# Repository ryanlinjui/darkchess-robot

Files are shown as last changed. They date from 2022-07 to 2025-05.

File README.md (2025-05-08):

> *"The project has been re-developing and refactoring since now." - 2024.11.12*  
> *"Now 'ONLY Brain Feature' is waiting for been completed......" - 2025.04.05*

# Darkchess Robot

<div align="center">

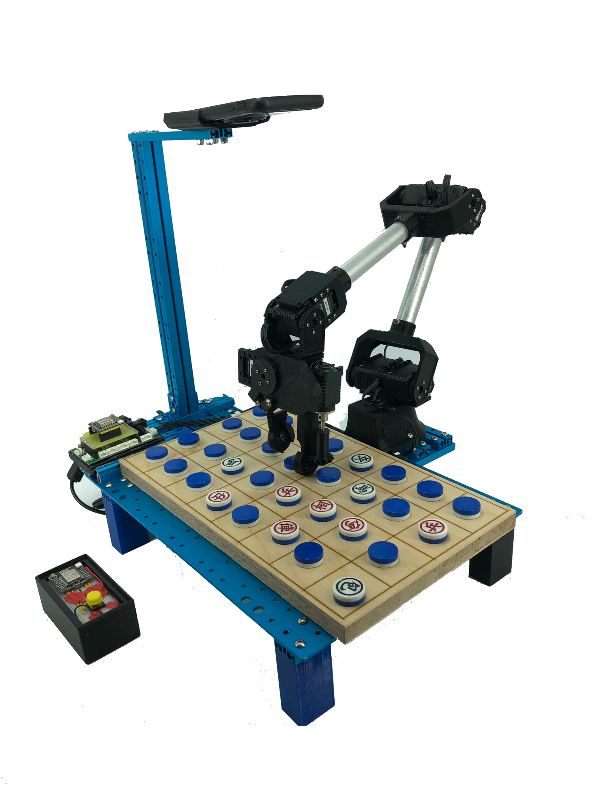
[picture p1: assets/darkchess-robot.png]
darkchess-robot
<br>

<br>
<br>
</div>

# 🤖 Demo

<div align="center">
  demo1
  demo2
</div>

# 💡 Getting Started
### Setup
Use [pixi](https://github.com/prefix-dev/pixi) to set up the development environment:

```
pixi shell
```

### Run Darkchess Robot System with Specific Mode
```bash
# Run Robot Server along with Website Monitor
python app.py --robot

# Run API Server of 'brain' & 'eye' Only
python app.py --api     
```
> Go [`config.py`](./config.py) to configure app settings before running server.

<div align="center">
  monitor
  sample-board
</div>

# 🚀 Features
## Brain - AI Engine for Darkchess Board Game
TBA......

## Eye – Real-World Detection and Recognition of Darkchess Board States
- **Model Architecture:** VGGNet-based darkchess board recognition
- **Training Accuracy:** 99.9%
- **Training Loss:** 7.2336e-06
- **Real-world Test Success Rate:** 98.9%

> For Eye training/testing script, refer to [`eye_train.ipynb`](./eye_train.ipynb).  
> Detailed model information is available on [Huggingface](https://huggingface.co/ryanlinjui/darkchess-robot-eye-VGGNet).

## Arm – Robotic Arm Control for Real-World Darkchess Applications
Our **Third-Generation Catcher** model with robotic arm that doing **Chess-Flipping** actions in Real-World Darkchess game.

> Explore the [Hardware](./arm/hardware) and [Firmware](./arm/firmware) for more details.

## AIoT – Darkchess Robot System Operable via WiFi
- API server collects training data from both Eye and Brain features. 
- Just a single button press starts gameplay via WiFi remote control.

> For API specifications, please see [documentation](https://github.com/ryanlinjui/darkchess-robot/wiki).

# 🌟 Awards 
- **Gold Medal (Int'l Top 50/408)** - 7th Kaohsiung International Invention & Design EXPO (2020)
- **Merit (Nat'l Top 20/661)** - [19th Macronix Science Awards (2020)](https://www.mxeduc.org.tw/scienceaward/history/projectDoc/19th/production.htm)
- **Second Place (Nat'l 2/200up)** - [12th i-ONE NARLabs Instrument Technology Innovation Competition (2020)](https://i-one.org.tw/Home/ListContents/107?ATimes=12)
- **Second Place in Engineering(I) (Nat'l 2/151)** - [60th National Primary and High School Science Fair (2020)](https://twsf.ntsec.gov.tw/activity/race-1/60/pdf/NPHSF2020-052310.pdf?746)
- **First Place in Engineering(I) (Reg)** - [53rd Taipei Primary and High School Science Fair (2020)](https://sites.google.com/csjh.tp.edu.tw/science/高級中等學校組/工程學科一?authuser=0#h.6xilplkz0fpy)
- **First Place in Engineering(I) (H.S.)** - Taipei Municipal Neihu Vocational High School Independent Study (2020)

# ®️ Patent
- **Invention Patent** - *DARK CHESS ROBOT (Dec 1, 2021) - TWI748780B*
- **Utility Model Patent** - *Robot arm gripper (Feb 21, 2021) - TWM608235U*

<div align="center">
  <a href="./assets/patent/TWI748780B.pdf">
    TWI748780B
  </a>
  <a href="assets/patent/TWM608235U.pdf">
    TWM608235U
  </a>
</div>
<br>

> Please visit [here](https://tiponet.tipo.gov.tw/gpss/) and search for the patent code as mentioned above.

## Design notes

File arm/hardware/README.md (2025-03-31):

# Hardware List

## Robotic Arm – 3D Models

<div align="center">
  arm-3d
  catcher-3d
</div>

- [Arm Catcher](./3D-models/catcher)
- [Arm Skeleton](./3D-models/skeleton)

> Designed by [Onshape](https://www.onshape.com)  
> The arm joints are powered by [XYZrobot Smart Servo A1-16](https://www.pololu.com/product/3400)

## Arm/Receiver System Development Boards

We have connected two boards:
- ATmega1280 board
- ESP8266 board

<div align="center">
  eda
  board
  board-2
</div>

> Designed by [EasyEDA](https://easyeda.com)  
> See [Firmware Code](../firmware) for details  

## Platform

darkchess-robot<br>

- [3D Models](./3D-models/platform)
- Materials provided by [Makeblock](https://www.makeblock.com)

## Remote Control

remote-control<br>

- [3D Models](./3D-models/remote)
- ESP8266 board
- Li-ion 18650 battery
- Breadboard
- Button module

> See [Firmware Code](../firmware) for details

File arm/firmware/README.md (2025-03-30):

# Getting Started

Update the following settings in the files **[remote_esp8266.ino](./remote_esp8266/remote_esp8266.ino), [receiver_esp8266.ino](./receiver_esp8266/receiver_esp8266.ino)**:

- **Server:** Set the IP address and port.
- **WiFi:** Configure the SSID and password.

> Note: ESP8266 supports only 2.4 GHz WiFi networks.

# Flashing Firmware
### Boards and FBQN

- [**Atmega1280**](https://www.microchip.com/wwwproducts/en/ATmega1280)
  - FBQN: `arduino:avr:mega:cpu=atmega1280`
- [**ESP8266**](https://github.com/esp8266/Arduino)
  - FBQN: `esp8266:esp8266:generic`

> **Note:** Check board’s FBQN using:  
> `arduino-cli board listall <board-name>`

### Install Core, Libraries
```bash
arduino-cli core install arduino:avr esp8266:esp8266 --config-file arduino-cli.yaml
arduino-cli lib install XYZrobotServo
```

### Attach & Set board
```
arduino-cli board attach --fqbn <your-fbqn> --port <your-usb-port-name> <your-sketch>
```
> **Note:** Find your USB port by:  
> `arduino-cli board list`

### Compile & Upload code
```
arduino-cli compile --upload <your-sketch>
```
> **(Optional)** Use the flag to define macros:  
> `--build-property build.extra_flags=-D<your-macro>` 

### Monitor Serial Output
```
arduino-cli monitor --config 115200 <your-sketch>
```

# Operating the Robotic Arm

| **Command** | **Description** | **Example** |
|:---:|:---:|:---:|
| **p (Park)** | Parks the arm in ininal area. | `p;` |
| **c (Catch)** | Catch / Grab action. | `c;` |
| **t (Turn)** | Turn over / Flip action. | `t;` | 
| **r (Release)** | Releases the held chess action. | `r;` |
| **m (Move)** | Moves the arm to specified coordinates (x, y, z). | `m -10,12,15;` |
| **x (X-axis)** | Adjusts the arm's position along the X-axis. | `x 15;` |
| **y (Y-axis)** | Adjusts the arm's position along the Y-axis. | `y 20;` |
| **z (Z-axis)** | Adjusts the arm's position along the Z-axis. | `z 10;` |
| **e (Eat)** | Eat the chess action | `e;` |
| **b (Buffer)** | Move to buffer middle area to reduce positional errors.  | `b;` |
| **d (Done)** | Print `done` as signal to response receiver system. | `d;` |

> Command are separated by **`;` semicolons**.  
> You can use **Monitor Serial** to operate.

### Example
- **Open Chess**
```
m 2.85,9.6,10;z 0.4;c;z 10;t;z 0.4;r;z 10;p;
```
> **Open chess at (21)**  
> If No.21 position at **(2.85, 9.6, 10 , bottom-z: 0.4)**

- **Move Chess**
```
m 6.5,14.3,10;z 0.9;c;z 10;b;m 10.1,19,10;z 1.8;r;z 10;p;
```
> **Move chess from (14) to (7)**  
> If No.14 position at **(6.5, 14.3, 10, bottom-z: 0.9)**  
> and No.7 position at **(10.1, 19, 10, bottom-z: 1.8)**

- **Eat Chess**
```
m -3.35,13.9,10;z 0.7;c;z 10;e;b;m -0.4,14,10;z 0.7;c;z 10;b;m -3.35,13.9,10;z 0.7;r;z 10;p;
```
> **Use chess at (12) to eat chess at (11)**  
> If No.11 position at **(-3.35, 13.9, 10, bottom-z: 0.7)**  
> and No.12 position at **(-0.4, 14, 10, bottom-z: 0.7)**

### Set / Change A1-16 Servo ID

Find example `ChangeId` in the library:

```
arduino-cli lib examples XYZrobotServo
```

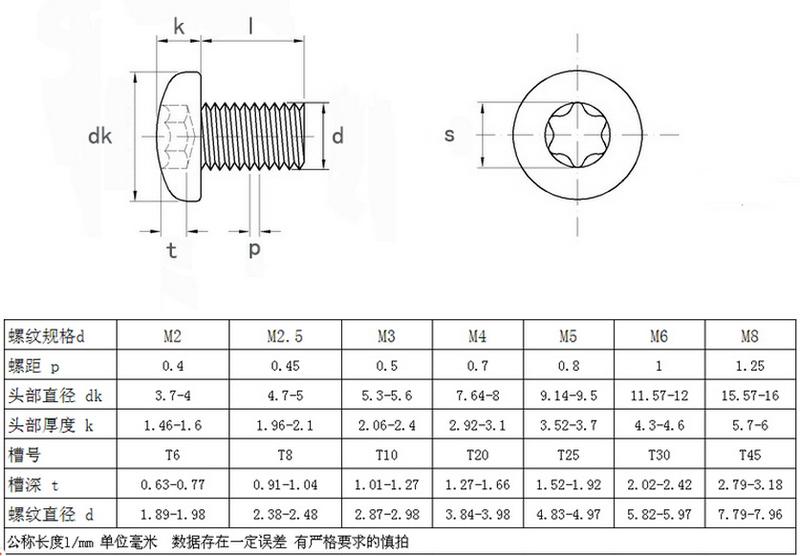
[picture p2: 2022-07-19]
arm/hardware/screw_spec.jpg

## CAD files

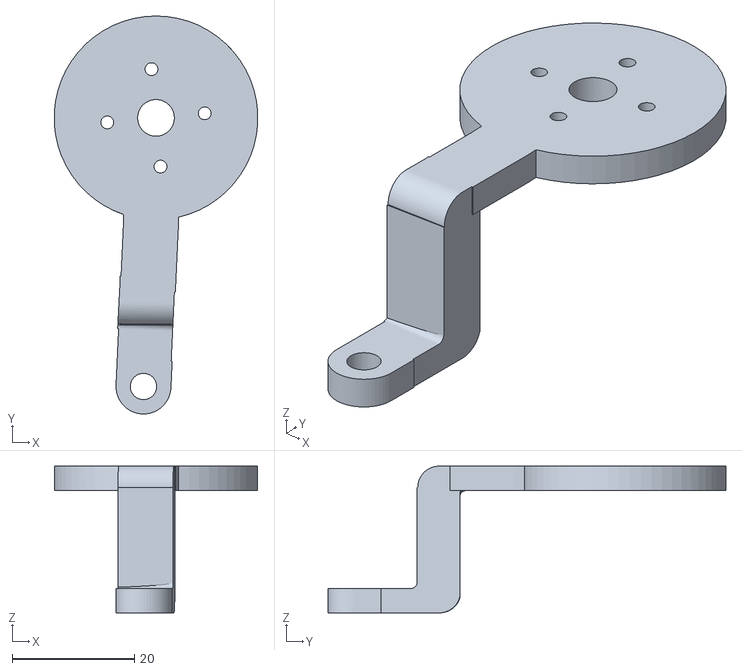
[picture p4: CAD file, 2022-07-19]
arm/hardware/3D-models/catcher/catcher_gear.stl
33.3 x 65.1 x 24.0

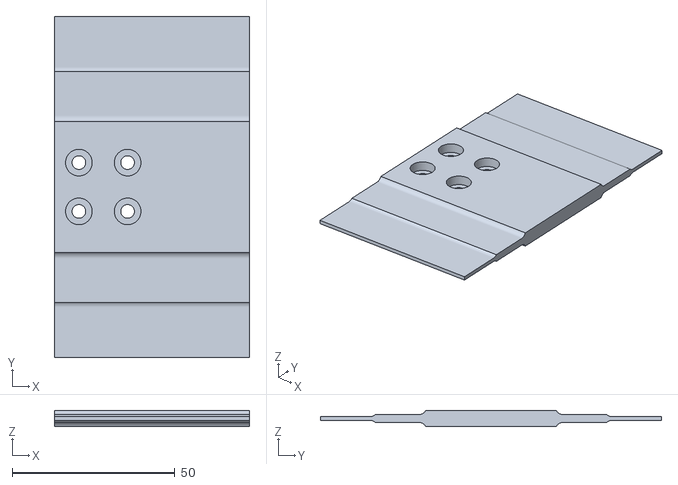
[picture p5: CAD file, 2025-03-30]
arm/hardware/3D-models/platform/PhoneCamera-bracket.stl
60.0 x 105.0 x 5.00

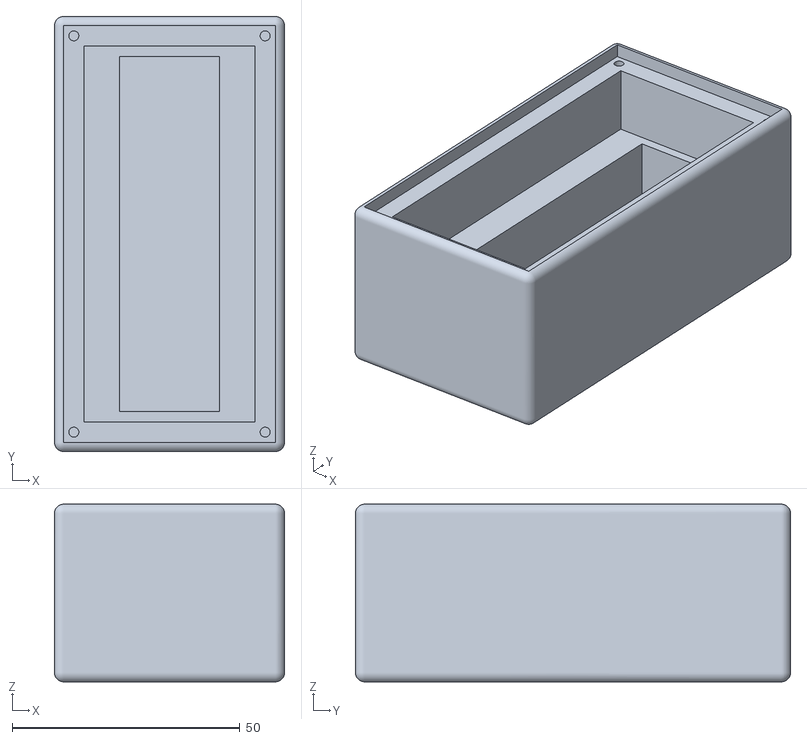
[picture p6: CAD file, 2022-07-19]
arm/hardware/3D-models/remote/remote_box.stl
50.5 x 95.5 x 39.0

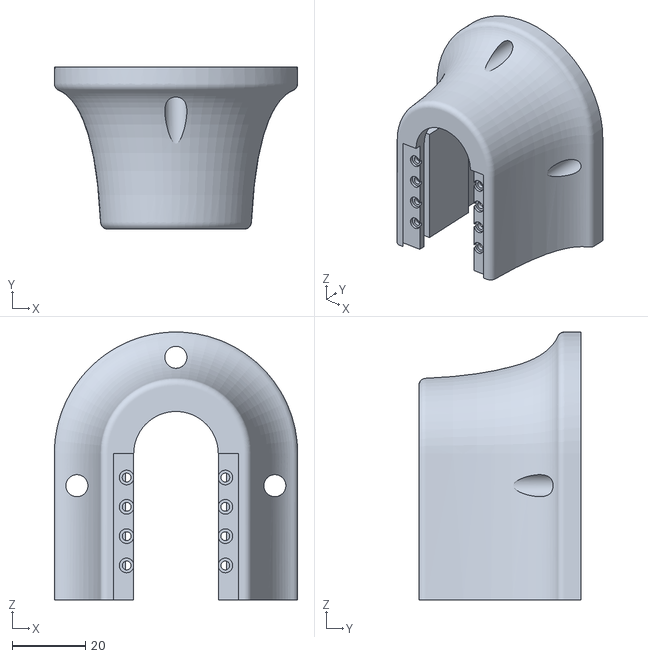
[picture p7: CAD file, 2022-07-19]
arm/hardware/3D-models/skeleton/motor_base.stl
66.4 x 44.3 x 73.1

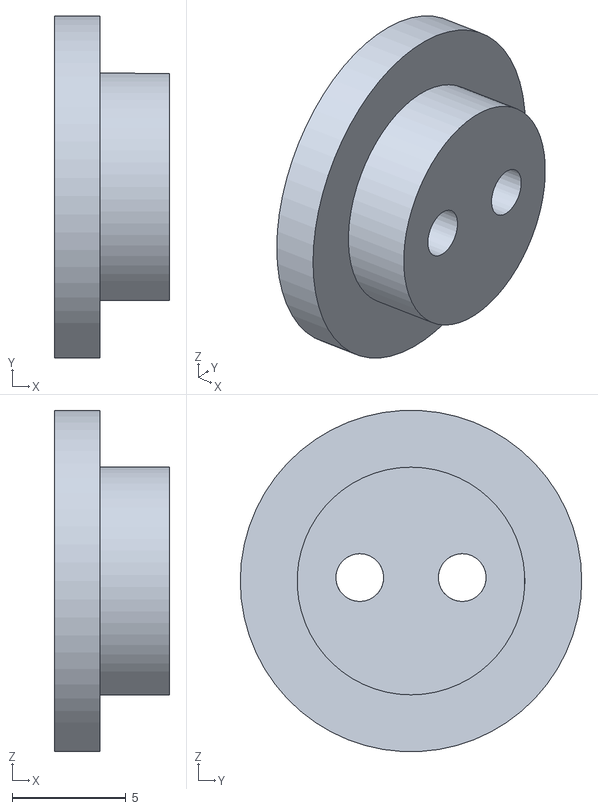
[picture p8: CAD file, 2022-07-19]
arm/hardware/3D-models/catcher/flip_support_fixed.stl
5.05 x 15.0 x 15.0

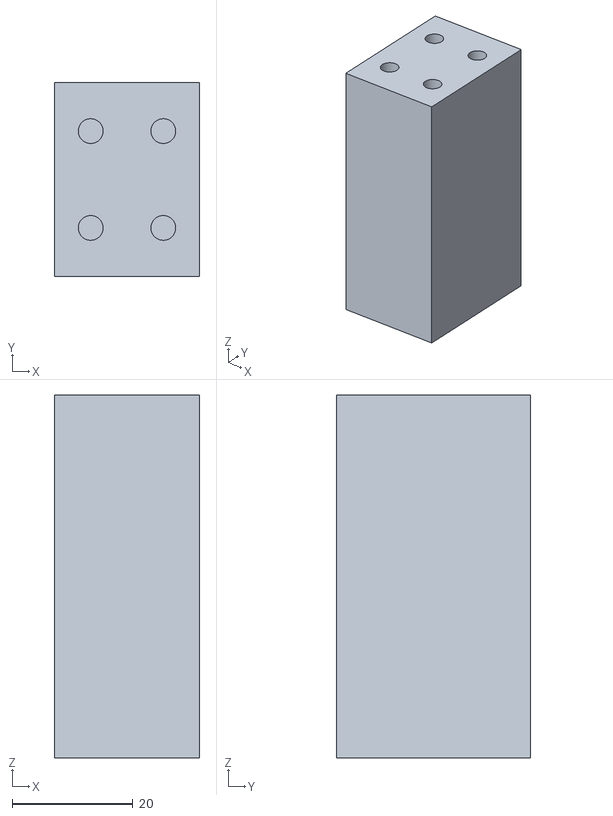
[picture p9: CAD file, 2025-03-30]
arm/hardware/3D-models/platform/platform-bracket.stl
24.0 x 32.0 x 60.0

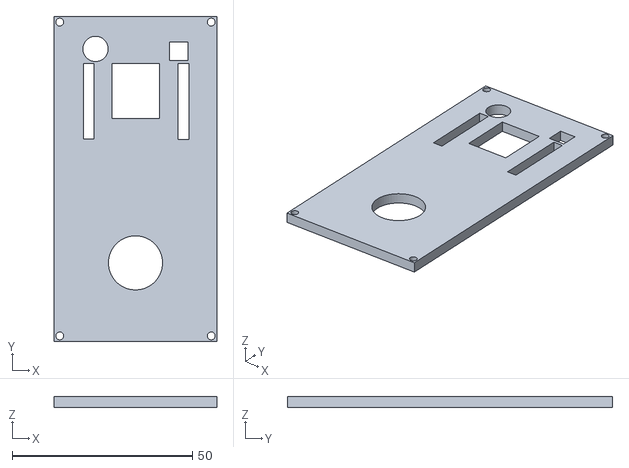
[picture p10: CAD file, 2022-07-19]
arm/hardware/3D-models/remote/cover_remote.stl
45.1 x 90.1 x 3.00

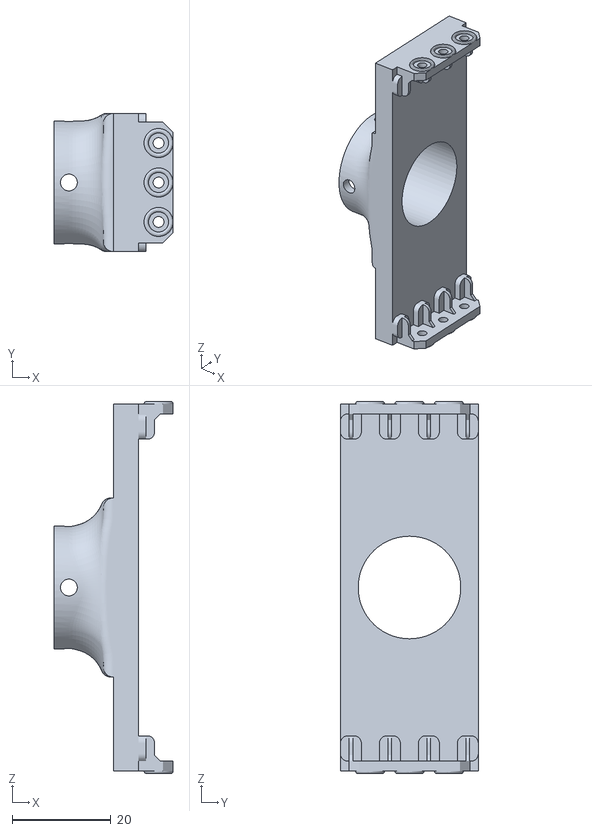
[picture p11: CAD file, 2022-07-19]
arm/hardware/3D-models/skeleton/double_pipe_board_connecter.stl
24.1 x 28.0 x 75.4

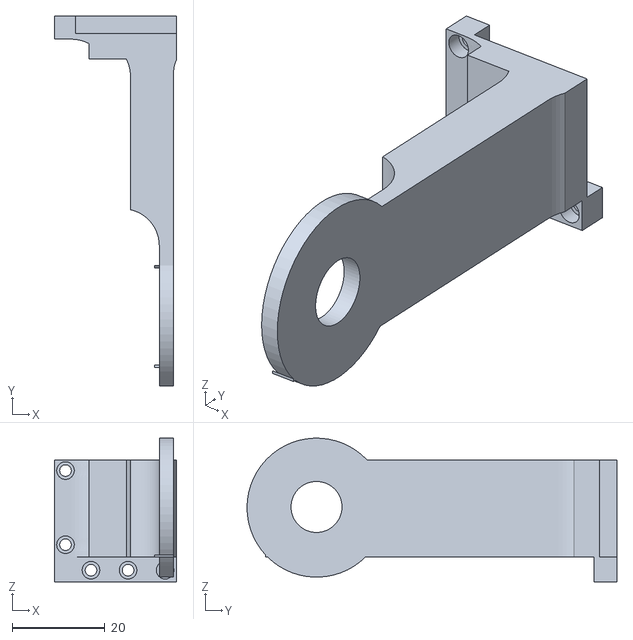
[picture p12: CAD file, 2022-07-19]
arm/hardware/3D-models/catcher/catcher_support_catch.stl
26.4 x 79.8 x 31.0

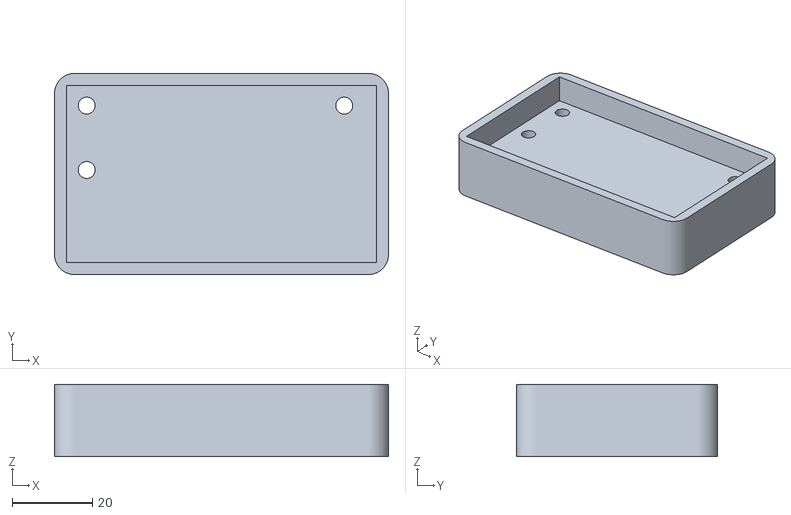
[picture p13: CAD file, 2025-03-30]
arm/hardware/3D-models/platform/circuit-board-case.stl
83.0 x 50.0 x 18.0

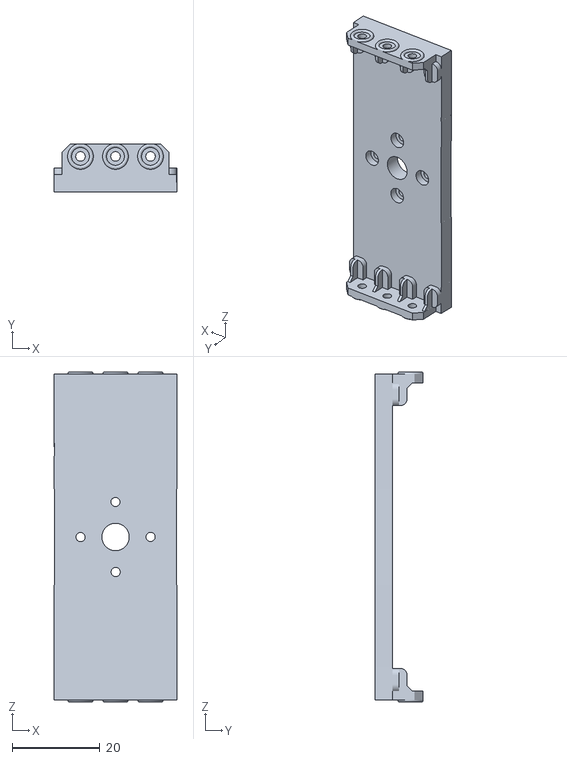
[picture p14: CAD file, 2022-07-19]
arm/hardware/3D-models/skeleton/double_board_connecter.stl
28.1 x 11.1 x 75.4

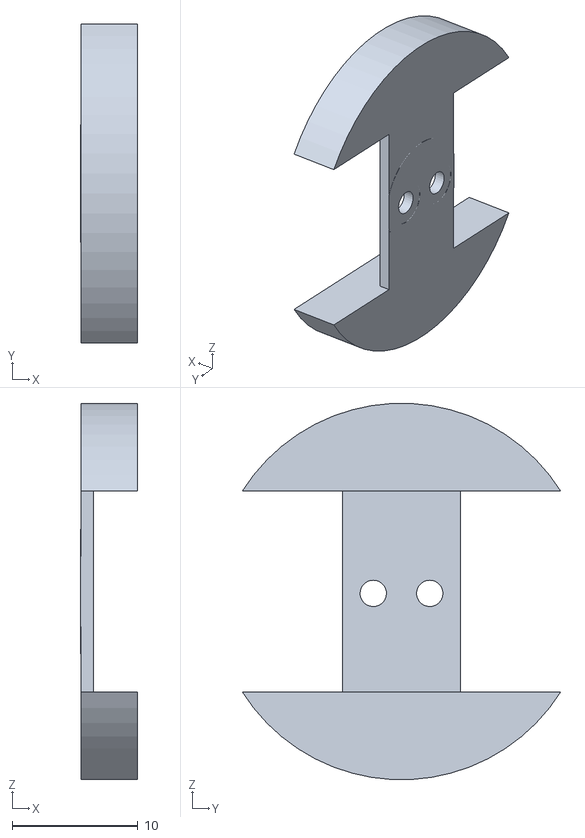
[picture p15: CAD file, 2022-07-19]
arm/hardware/3D-models/catcher/flip_passive.stl
4.52 x 25.4 x 30.0

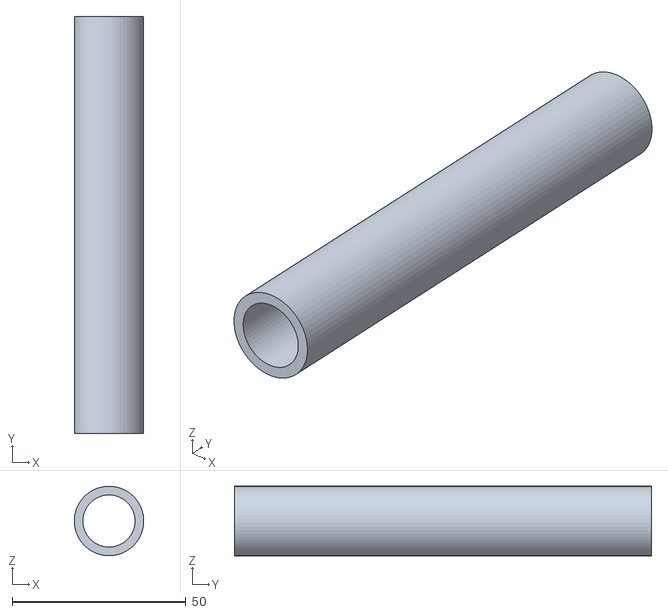
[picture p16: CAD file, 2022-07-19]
arm/hardware/3D-models/skeleton/pipe.stl
20.0 x 120.0 x 20.0

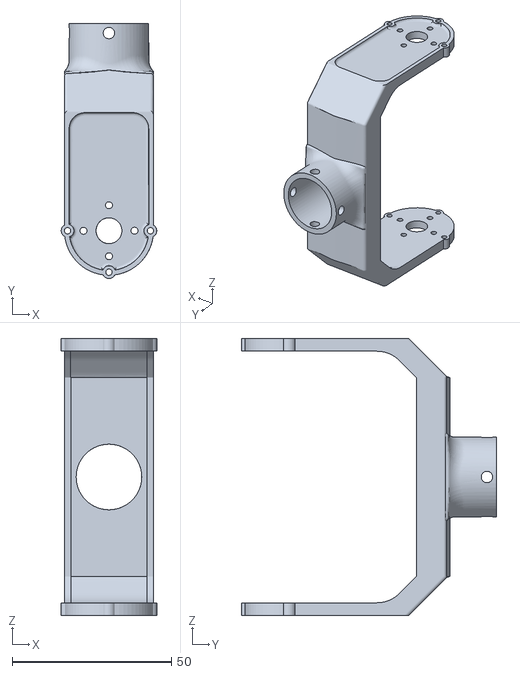
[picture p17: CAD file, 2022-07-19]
arm/hardware/3D-models/skeleton/double_clip_connecter.stl
30.0 x 80.1 x 87.0

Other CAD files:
arm/hardware/3D-models/catcher/flip_proactive.stl
arm/hardware/3D-models/catcher/beveled_gear.stl
arm/hardware/3D-models/skeleton/cover_base.stl
arm/hardware/3D-models/catcher/catcher_platform.stl
arm/hardware/3D-models/catcher/catcher_catch.stl
arm/hardware/3D-models/catcher/catcher_support.stl
arm/hardware/3D-models/catcher/darkchess.stl
arm/hardware/3D-models/catcher/flip_cylinder.stl
arm/hardware/3D-models/skeleton/covered_connecter.stl

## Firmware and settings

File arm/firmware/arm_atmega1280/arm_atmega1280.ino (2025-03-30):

#include <XYZrobotServo.h>

#ifdef SERIAL_PORT_HARDWARE_OPEN
    #define servoSerial SERIAL_PORT_HARDWARE_OPEN
#else
    #include <SoftwareSerial.h>
    SoftwareSerial Serial1(10, 11);
#endif

// ==============================================
// Please visit Research Report link at README.md
// ==============================================

// Set servo ID on each arm joint
XYZrobotServo servo1(Serial1, 1);
XYZrobotServo servo2_a(Serial1, 2);
XYZrobotServo servo2_b(Serial1, 7); 
XYZrobotServo servo3_a(Serial1, 3); 
XYZrobotServo servo3_b(Serial1, 8); 
XYZrobotServo servo4(Serial1, 4);
XYZrobotServo servo5(Serial1, 5);
XYZrobotServo servo6(Serial1, 6);

// Set the arm length of the robot arm (unit: cm)
#define ARM_LENGTH_ALPHA 19.5
#define ARM_LENGTH_BETA 22.3
#define ARM_LENGTH_DEPTH 15.7
#define ARM_LENGTH_HEIGHT 5.5
// ==============================================

float servo_deg = (float)1024 / 330;
int playtime = 150;

enum E_CMD {P, C, T, R, M, X, Y, Z, E, B, D};
String CMD[11] = {"P", "C", "T", "R", "M", "X", "Y", "Z", "E", "B", "D"};

int target[4] = {0, 0, 0, 0};
float tx = 0, ty = 0, tz = 0;
int turn_num = 640;
int turn180 = 290;

int searchCommand(String cmd);
void park();
int Degree2Steps(int id, double degree);
void move_xyz(float x, float y, float z);
void show(float theta[4], int target[4]);
void servo_turn(int servo_num, int degree);
float GetData(String data, int i);
String GetDataStr(String data, int i);

int searchCommand(String cmd)
{
    for(int i = 0; i < 11; i++)
    {
        if(cmd == CMD[i])
        {
            return i;
        }
    }
    return 0;
}

void park()
{
    tx = -7;
    ty = 1;
    tz = 10;
    move_xyz(tx, ty, tz);
    servo_turn(6, 430);
}

int Degree2Steps(int id, double degree)
{
    int servo[4] = {233, 791, 791, 1024}; // 0, 180, 180
    return servo[id] - degree * servo_deg;
}

void move_xyz(float x, float y, float z)
{
    // ========== Arm Formula ==========
    float a = ARM_LENGTH_ALPHA; // arm argument
    float b = ARM_LENGTH_BETA; // arm argument
    float d = ARM_LENGTH_DEPTH; // arm argument
    
    float h = ARM_LENGTH_HEIGHT;
    float s = h - z;
    float e = d - s;
    float l = sqrt(x * x + y * y);
    float c = sqrt(e * e + l * l); 
    // =================================

    float theta[4] = {0, 0, 0, 0};
    theta[0] = atan2(y, x) * 180 / PI; // Polar Coordinate

    // ======================= Law of Cosines =======================
    theta[3] = (acos((c * c + e * e - l * l) / (2 * c * e)) * 180 / PI) + 
                (acos((b * b + c * c - a * a) / (2 * b * c)) * 180 / PI);
                    
    theta[2] = acos((a * a + b * b - c * c) / (2 * a * b)) * 180 / PI;
    theta[1] = 360 - theta[3] - theta[2];
    // ==============================================================
    
    target[0] = Degree2Steps(0, -theta[0]); 
    target[1] = Degree2Steps(1, theta[1]); 
    target[2] = Degree2Steps(2, theta[2]); 
    target[3] = Degree2Steps(3, theta[3]); 
    show(theta, target);
    
    // Check if the theta is NaN
    for(int i = 3; i >= 0; i--)
    {
        if(isnan(theta[i]))
        {
            return;
        }
    }
    
    int order[4]{3, 4, 2, 1};
    for(int i = 0; i < 4; i++)
    {
        servo_turn(order[i], target[order[i] - 1]);
    }
    // delay(200);
}

void show(float theta[4], int target[4])
{
    for(int i = 0; i < 4; i++)
    {
        Serial.print(i + 1);
        Serial.print(": theta:");
        Serial.print(theta[i]);
        Serial.print(" target:");
        Serial.println(target[i]);
    }
    Serial.println();
}

void servo_turn(int servo_num, int degree)
{
    switch(servo_num)
    {
        case 1:
            servo1.setPosition(degree, playtime);
            break;
        
        case 2:
            servo2_a.setPosition(degree, playtime);
            servo2_b.setPosition(1024 - degree, playtime);
            break;

        case 3:
            servo3_a.setPosition(degree, playtime);
            servo3_b.setPosition(1024 - degree, playtime);
            break;
        
        case 4:
            servo4.setPosition(degree, playtime);
            break;        

        case 5:        
            servo5.setPosition(degree, playtime);
            break;
        
        case 6:
            if(degree >= 430 && degree <= 570)
            {
                servo6.setPosition(degree, playtime);
            }
            break;
        
        default:
            break;
    }
}

float GetData(String data, int i)
{
    int count = 0;
    String getdata = "";

    while(count <= i)
    {
        getdata = data.substring(0, data.indexOf(','));
        data = data.substring(data.indexOf(',') + 1);
        count++;
    }
    return getdata.toFloat();
}

String GetDataStr(String data, int i)
{
    int count = 0;
    String getdata = "";
    
    while(count <= i)
    {
        getdata = data.substring(0, data.indexOf(','));
        data = data.substring(data.indexOf(',') + 1);
        count++;
    }
    return getdata;
}

void setup()
{
    Serial1.begin(115200);
    Serial.begin(115200);
    playtime = 150;
    servo_turn(5, 350);
    park();
}

void loop()
{
    String temp_cmd = "";
    String temp_data = "";
    
    if(Serial.available()) 
    {
        temp_cmd = Serial.readString();    
        temp_cmd.replace("\n", "");
        temp_cmd.replace("\r", "");
    }

    while(temp_cmd.indexOf(';') != -1)
    {
        temp_data = temp_cmd.substring(0, temp_cmd.indexOf(';'));
        temp_cmd.remove(0, temp_cmd.indexOf(';') + 1);
        
        String cmd = temp_data.substring(0, temp_data.indexOf(' '));
        String data = temp_data.substring(temp_data.indexOf(' ') + 1);

        cmd.toUpperCase();
        Serial.println(temp_data);
        switch(searchCommand(cmd))
        {
            case P:
            {
                playtime = 150;
                park();
                break;
                
            }
            
            case C:   
            {
                playtime = 150;
                //servo_turn(6, 548);
                servo_turn(6, 560);
                break;
            }

            case T:
            {
                playtime = 100;
                servo_turn(5, turn_num + turn180);
                turn180 *= -1;
                break;
            }

            case R:
            { 
                playtime = 150;
                servo_turn(6, 430);
                break;
            }

            case M:
            {
                playtime = 120;
                tx = GetDataStr(data, 0) != "" ? GetData(data, 0) : tx;
                ty = GetDataStr(data, 1) != "" ? GetData(data, 1) : ty;
                tz = GetDataStr(data, 2) != "" ? GetData(data, 2) : tz;
                move_xyz(tx, ty, tz);
                break;
            }
        
            case X:
            { 
                playtime = 90;
                tx = GetData(data, 1);
                move_xyz(tx, ty, tz);
                break;
            }
            
            case Y:
            {  
                playtime = 90;
                ty = GetData(data, 1);
                move_xyz(tx, ty, tz);
                break;
            }
            
            case Z:
            {
                playtime = 90;
                tz = GetData(data, 1);
                move_xyz(tx, ty, tz);
                break;
            }

            case E:
            {
                playtime = 100;
                move_xyz(-18, 1, 7);
                delay(2200);
                playtime = 150;
                servo_turn(6, 430);
                break;
            }

            case B:
            {
                playtime = 120;
                move_xyz(1, 10, 10);
                break;
            }

            case D:
            {
                Serial.println("done");
                break;
            }
            
            default:
            {
                break;
            }
        }
        delay(3000);
    }
}

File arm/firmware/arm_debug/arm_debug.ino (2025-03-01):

#include <XYZrobotServo.h>

#ifdef SERIAL_PORT_HARDWARE_OPEN
    #define servoSerial SERIAL_PORT_HARDWARE_OPEN
#else
    #include <SoftwareSerial.h>
    SoftwareSerial Serial1(10, 11);
#endif

XYZrobotServo servo1(Serial1, 1); 
XYZrobotServo servo2_a(Serial1, 2);
XYZrobotServo servo3_a(Serial1, 3);
XYZrobotServo servo4(Serial1, 4); 
XYZrobotServo servo5(Serial1, 5);
XYZrobotServo servo6(Serial1, 6);
XYZrobotServo servo2_b(Serial1, 7);
XYZrobotServo servo3_b(Serial1, 8);

const uint8_t playtime = 150; // turn speed
const uint8_t turntime = 255;

void regular()
{
    servo1.setPosition(512, playtime); // regular: 512
    // servo2.setPosition(335, playtime); // regular: 120, min: 100 max: 480
    // servo3.setPosition(676, playtime); // regular: 620, min: 100 max: 750
    // servo4.setPosition(335, playtime); // regular: 790, turn 0 to 180 (790 ~ 240)
    // servo5.setPosition(512, playtime); // regular: 512, ID: 11
    // servo6.setPosition(430, playtime); // regular: 165, min: 165, max: 300 ID: 8
}

void setup()
{
    Serial1.begin(115200); // motor
    Serial.begin(115200);  // tx/rx
    regular();
}

void loop()
{
    if (Serial.available())
    { 
        String communication = Serial.readString(); 
        int servonum = communication.substring(0, 1).toInt();
        int degree = communication.substring(2, 6).toInt();  
        
        Serial.println("communication = ");
        Serial.println(communication);  
        Serial.println("servonum = ");
        Serial.println(servonum);
        Serial.println("degree = ");
        Serial.println(degree);
        
        switch(servonum)
        {
            case 1:
                servo1.setPosition(degree, playtime); 
                break;
                
            case 2:
                servo2_a.setPosition(degree, playtime);
                servo2_b.setPosition(1024 - degree, playtime);
                break;

            case 3:
                servo3_a.setPosition(degree, playtime);
                servo3_b.setPosition(1024 - degree, playtime);
                break;

            case 4:
                servo4.setPosition(degree, playtime);
                break;
            
            case 5:
                servo5.setPosition(degree, turntime);
                break;

            case 6:
                if(degree >= 400 && degree <= 600)
                {
                    servo6.setPosition(degree, playtime);
                    break;
                }
                else
                {
                    Serial.println("No");
                }
                
            default:
                break;
        }
    }
}

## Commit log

2022-07-19 docs: arm's readme needed img
2022-07-19 feat: arm model source files
    [beveled_gear.stl, catcher_catch.stl, catcher_gear.stl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]
2022-07-19 feat: raspberry pi a1-16 motor drive
2022-07-19 docs: A1-16 motor documents
2022-07-19 feat: arm postion source file
2022-07-19 feat: arm auto set position file
2022-07-19 feat: arm drive
2022-07-19 feat: test arm file
2023-08-22 refactor: arm direcory re-architect
2025-03-07 refactor: init
    [beveled_gear.stl, catcher_catch.stl, catcher_gear.stl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]
2025-03-26 feat: arm battle process
2025-03-27 feat: add platform 3D printing
    [PhoneCamera-bracket.stl, circuit-board-case.stl, platform-bracket.stl]
2025-03-28 docs: improve info, add arm command infos
2025-03-30 feat: arm firmware
2025-03-30 fix: get one frame from image, get chess frame 0 shape issue
2025-03-30 feat: arm command
2025-04-04 docs: eye, arm, aiot feature info, getting started info
2025-04-15 feat: learning agent prototype
2025-04-21 feat: ql prototype
2026-02-27 refactor(brain): add canonical board encoding utilities and move state encoding to agents
2026-02-27 fix: mask more chess for full-board ql
2026-02-28 fix: more mask chess for ql agent full board
